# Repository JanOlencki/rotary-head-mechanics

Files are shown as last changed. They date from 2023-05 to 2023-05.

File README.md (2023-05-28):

# Mechanics of the Rotary Head
This repository is a part of a larger project. The description of it can be found in the [rotary-head-software](https://github.com/JanOlencki/rotary-head-software) repository.

## Features
* Two heads (azimuth and polarization)
* Stepper motor mounting
* Smooth rotation due to ball bearings
* 1:3.6 gear ratio (0.5° resolution when fully stepping a 200-step motor)
* Geodesy tribrach mounting
* Precise tribrach-based leveling
* RF connection via *Fairview Microwave SR1803* rotary joint
* Easily removable enclosure
* Enclosure compatible with the [Rotary Head Controller PCBs](https://github.com/JanOlencki/rotary-head-electronics)
* Laser holders used to position towers relative to each other

## Manufacturing
The original milled parts are made from nylon and steel without the use of numerically controlled machines. There are no tolerances marked or introduced in the models of these parts.

The enclosures and holders are printed from PETG. The models of the 3D printed parts include small gaps, that allows you to simply print and fit these parts with virtually no modification.

## Repository contents
* Separate Bills of Materials for each Rotary Head
* Models of the milled parts in the STEP format
* Models of the 3D printed parts in the STEP format
* Photos and renders

# Photos 
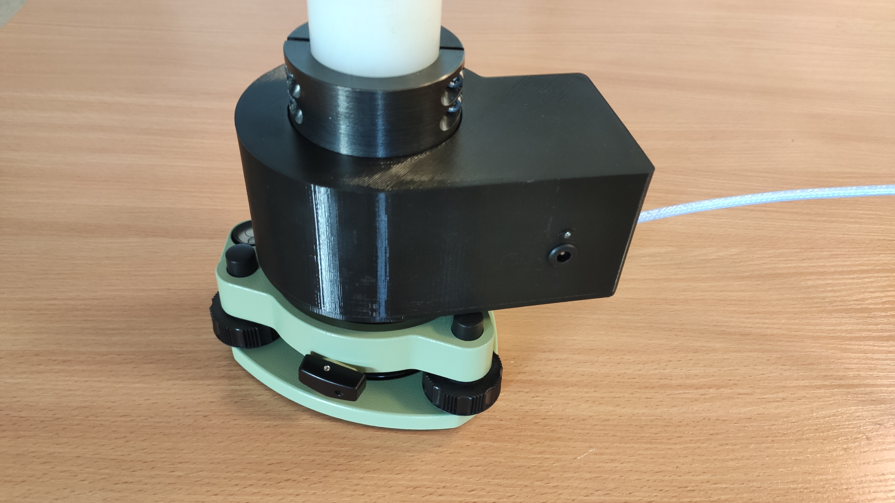
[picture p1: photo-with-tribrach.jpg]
Photo of the azimuth Rotary Head on the tribrach


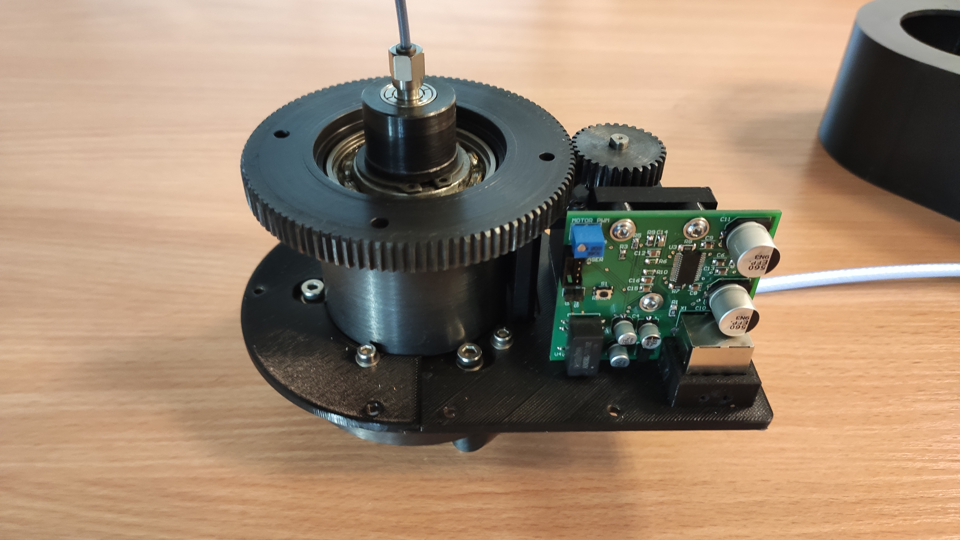
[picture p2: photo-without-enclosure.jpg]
Photo of the azimuth Rotary Head without enclosure


# Renders
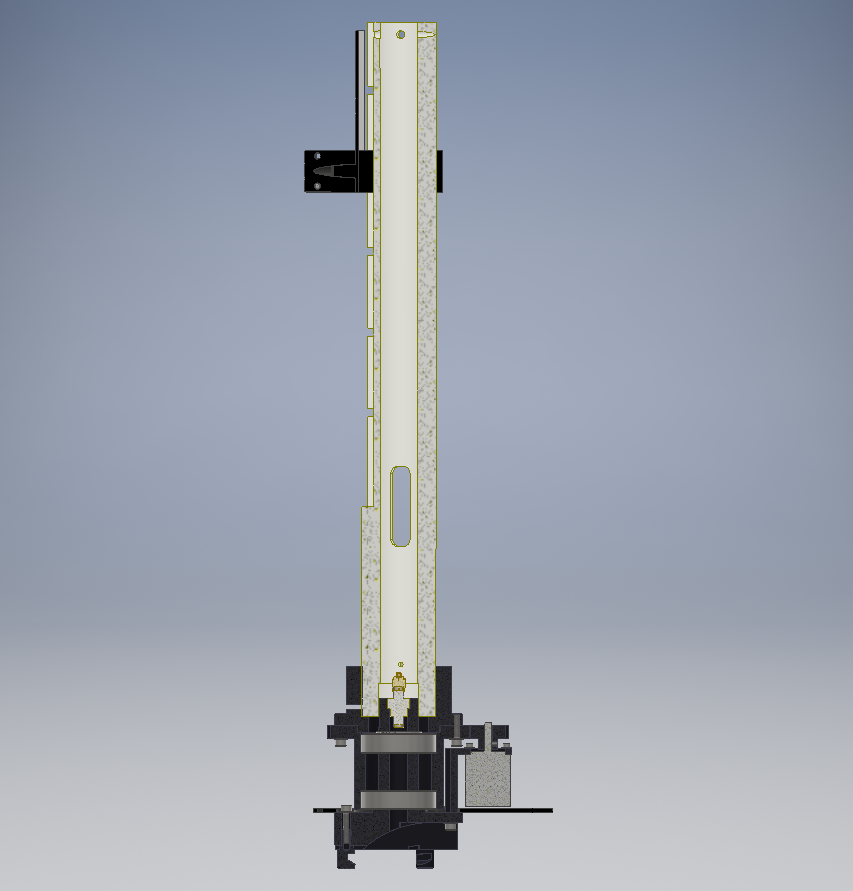
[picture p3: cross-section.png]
The cross section of Rotary Head


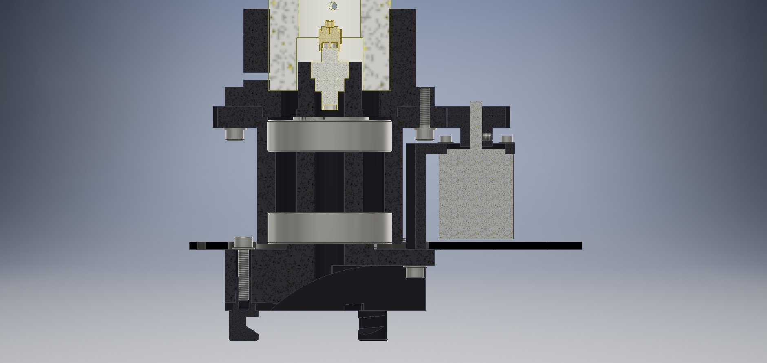
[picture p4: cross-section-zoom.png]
The zoomed cross section of Rotary Head


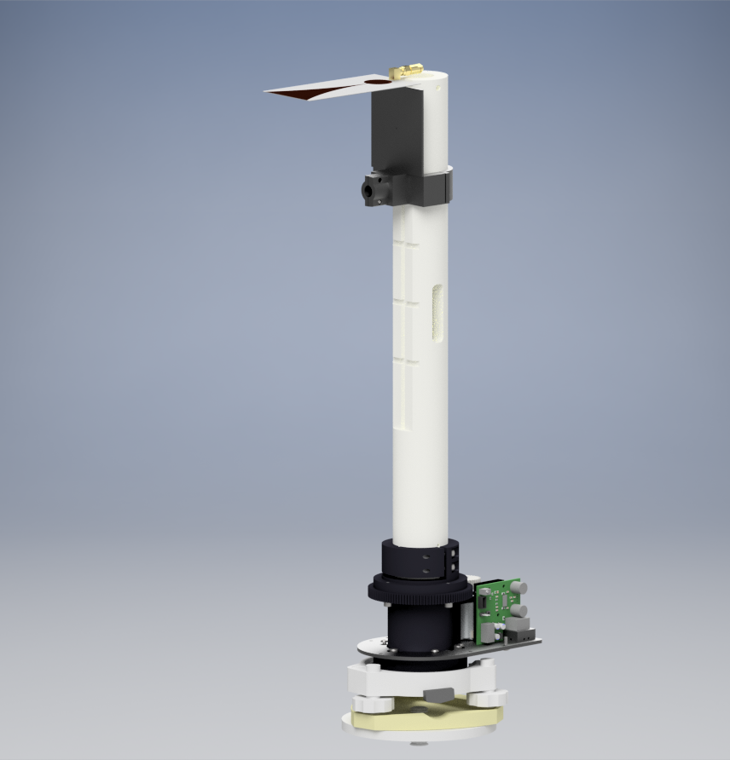
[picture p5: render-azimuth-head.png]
The render of the azimuth Rotary Head


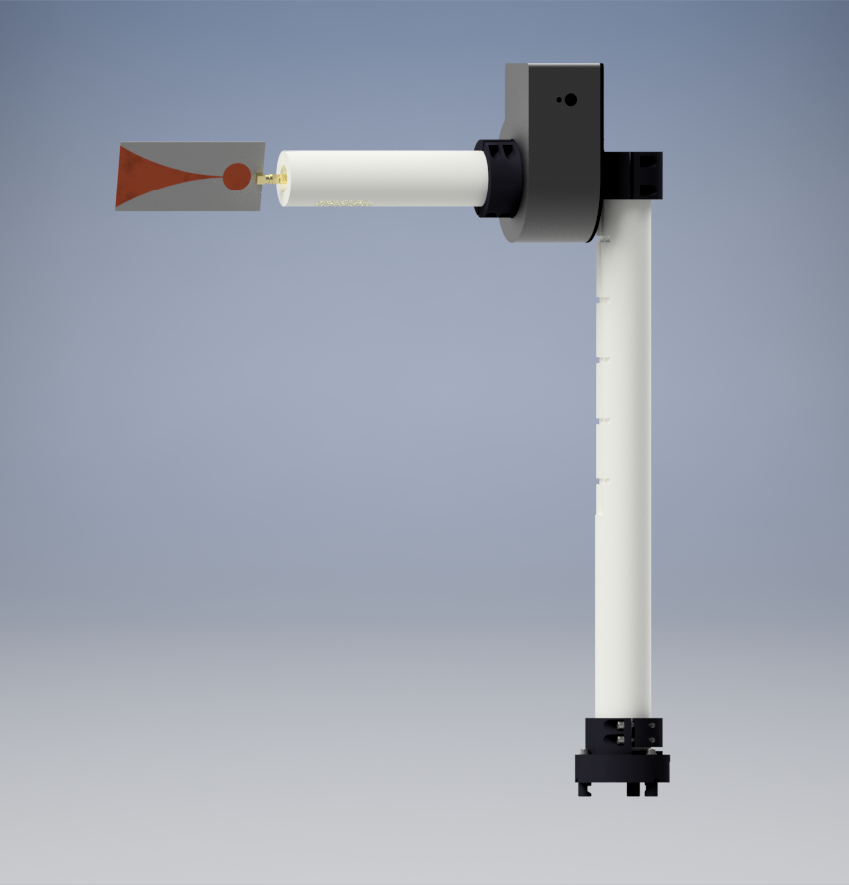
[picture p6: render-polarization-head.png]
The render of the polarization Rotary Head


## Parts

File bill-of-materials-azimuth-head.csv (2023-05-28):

Name | Quantity | Description | Comment
Flanged Button Screw M3 x 10mm (ISO 7380-2) | 15 | Used to screw the enclosure and milled parts together
Flanged Button Screw M3 x 10mm (ISO 7380-2) | 10 | Laser holder | Optional
Bearing 6005 - 25mm x 47mm x 12mm (DIN 625 - T1) | 2
Retaining ring 25mm x 1.2mm (DIN 471) | 1
Bolt M4 x 20mm (DIN 912) | 9
Bolt M4 x 16mm (DIN 912) | 4 | Used to bolt the outer sleeve and shaft holder together
Plain washer 4.3mm (DIN 125-1) | 13
Step motor Pololu 1205 | 1
Socket set screw M3 x 4mm (DIN 913) | 2 | Used to hold the rotary joint and to mount the gear to the motor shaft
Bolt M2.5 x 8mm (DIN 912) | 4 | Used to mount the motor
Plain washer 2.7mm (DIN 125-1) | 4
Rotary joint SR1803 | 1
Azimuth head shaft | 1 | Milled nylon part
Sleeve with gear | 1 | Milled steel part
Azimuth head tribrach adapter | 1 | Milled steel part
Gear | 1 | Milled steel part
Motor mount | 1 | Milled steel part
Shaft mount | 1 | Milled steel part
Tribrach stud | 3 | Milled steel part
Azimuth head enclosure bottom part 1 | 1 | 3d printed part
Azimuth head enclosure bottom part 2 | 1 | 3d printed part
Head enclosure top | 1 | 3d printed part
PCB holder | 1 | 3d printed part
Laser holder part 1 | 1 | 3d printed part | Optional
Laser holder part 2 | 1 | 3d printed part | Optional
Laser holder part 3 | 1 | 3d printed part | Optional
Laser holder part 4 | 1 | 3d printed part | Optional
Laser holder part 5 | 1 | 3d printed part | Optional

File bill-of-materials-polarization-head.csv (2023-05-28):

Name | Quantity | Description | Comment
Flanged Button Screw M3 x 10mm (ISO 7380-2) | 15 | Used to screw the enclosure and milled parts together
Flanged Button Screw M3 x 10mm (ISO 7380-2) | 10 | Laser holder | Optional
Bearing 6005 - 25mm x 47mm x 12mm (DIN 625 - T1) | 2
Retaining ring 25mm x 1.2mm (DIN 471) | 1
Bolt M4 x 20mm (DIN 912) | 13
Bolt M4 x 16mm (DIN 912) | 4 | Used to bolt the outer sleeve and shaft holder together
Plain washer 4.3mm (DIN 125-1) | 17
Step motor Pololu 1205 | 1
Socket set screw M3 x 4mm (DIN 913) | 2 | Used to hold the rotary joint and to mount the gear to the motor shaft
Bolt M2.5 x 8mm (DIN 912) | 4 | Used to mount the motor
Plain washer 2.7mm (DIN 125-1) | 4
Rotary joint SR1803 | 1
Polarization head vertical shaft | 1 | Milled nylon part
Polarization head horizontal shaft long | 1 | Milled nylon part
Polarization head horizontal shaft medium | 1 | Milled nylon part | Optional
Polarization head horizontal shaft short | 1 | Milled nylon part | Optional
Sleeve with gear | 1 | Milled steel part
Polarization head tribrach adapter | 1 | Milled steel part
Polarization head central part | 1 | Milled steel part
Gear | 1 | Milled steel part
Motor mount | 1 | Milled steel part
Shaft mount | 1 | Milled steel part
Tribrach stud | 3 | Milled steel part
Polarization head enclosure bottom part 1 | 1 | 3d printed part
Polarization head enclosure bottom part 2 | 1 | 3d printed part
Head enclosure top | 1 | 3d printed part
PCB holder | 1 | 3d printed part
Laser holder part 1 | 1 | 3d printed part | Optional
Laser holder part 2 | 1 | 3d printed part | Optional
Laser holder part 3 | 1 | 3d printed part | Optional
Laser holder part 4 | 1 | 3d printed part | Optional
Laser holder part 5 | 1 | 3d printed part | Optional

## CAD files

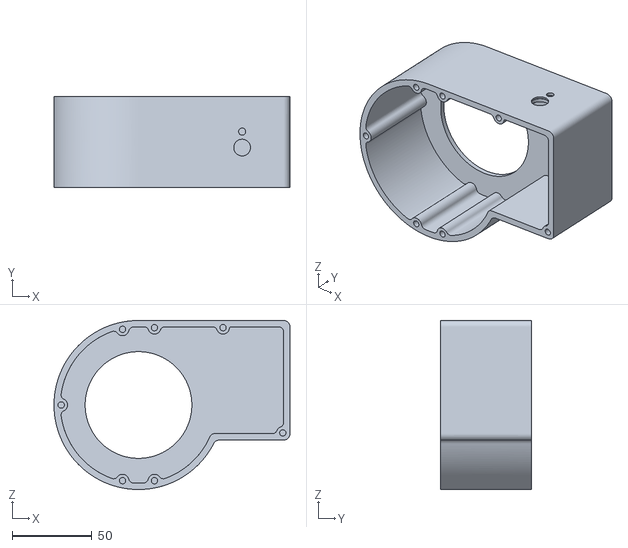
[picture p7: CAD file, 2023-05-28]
3d-printed/head-enclosure-top.stl
148.0 x 57.0 x 106.0

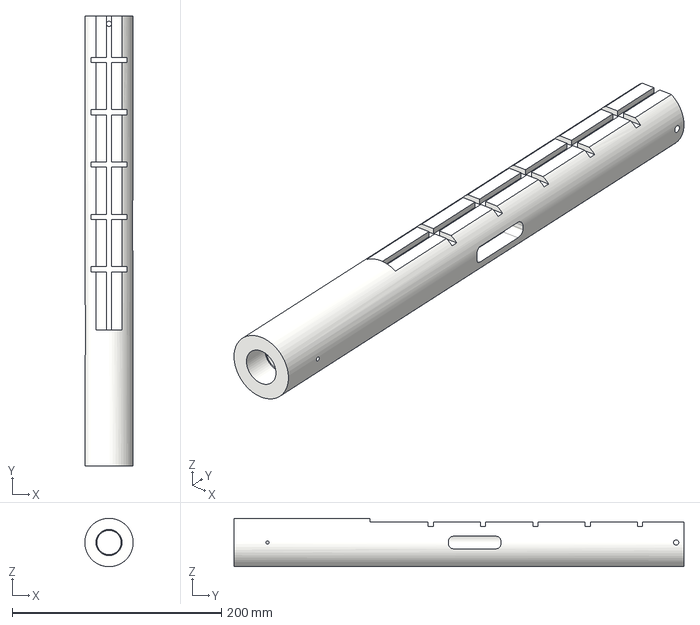
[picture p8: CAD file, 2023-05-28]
milled-parts/azimuth-head-shaft.stp
46.2 x 430.0 x 46.2 mm

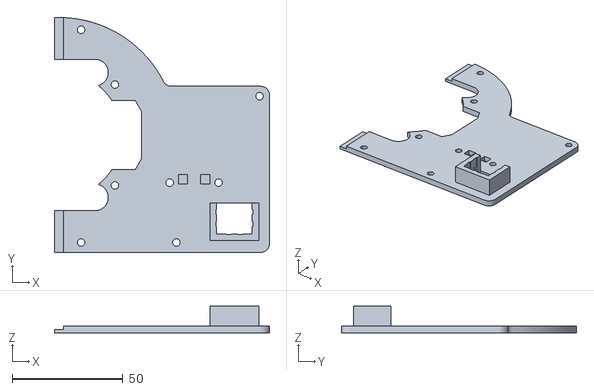
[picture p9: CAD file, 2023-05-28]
3d-printed/azimuth-head-enclosure-bottom-part-1.stl
97.0 x 106.0 x 12.0

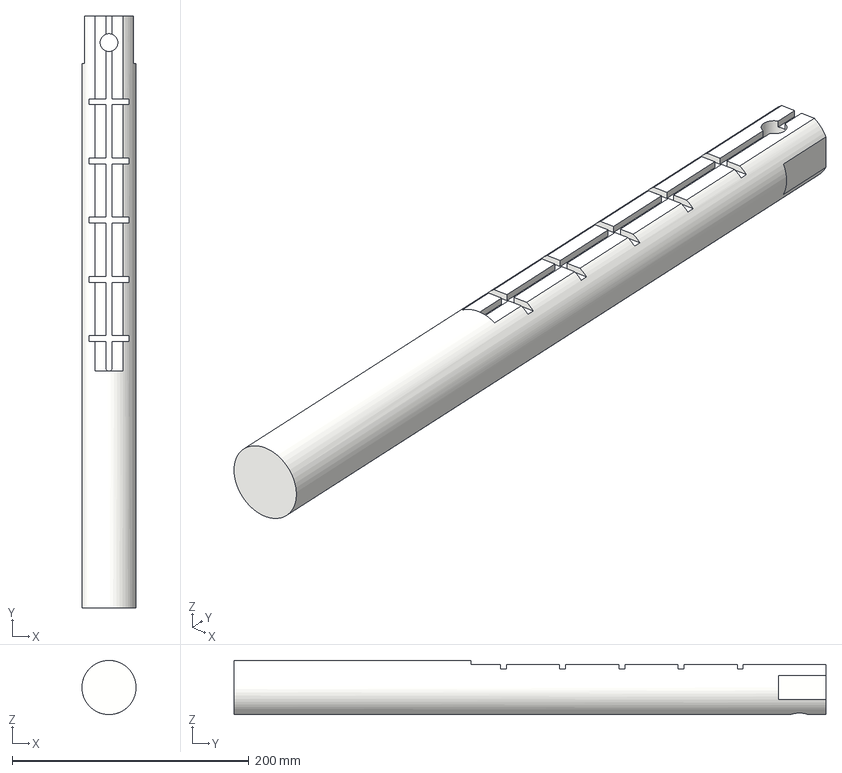
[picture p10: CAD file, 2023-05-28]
milled-parts/polarization-head-vertical-shaft.stp
45.8 x 500.0 x 45.7 mm

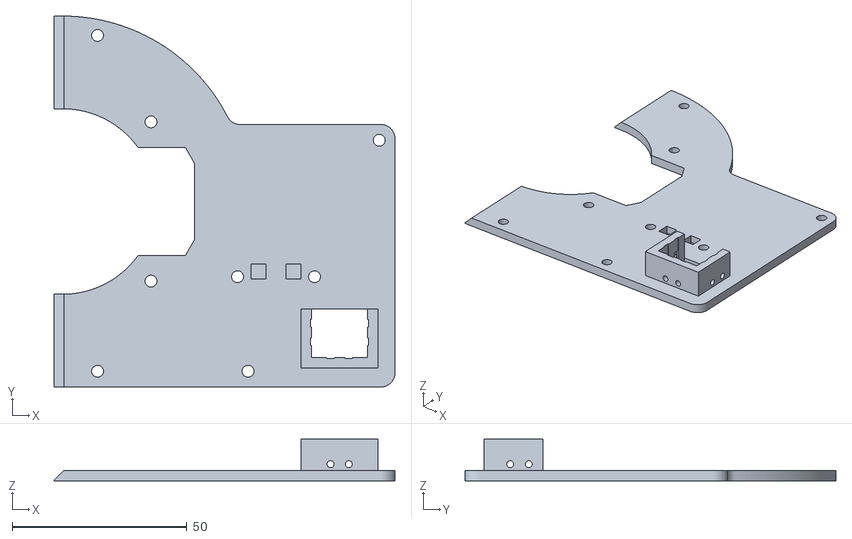
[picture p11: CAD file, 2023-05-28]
3d-printed/polarization-head-enclosure-bottom-part-1.stl
97.5 x 106.0 x 12.0

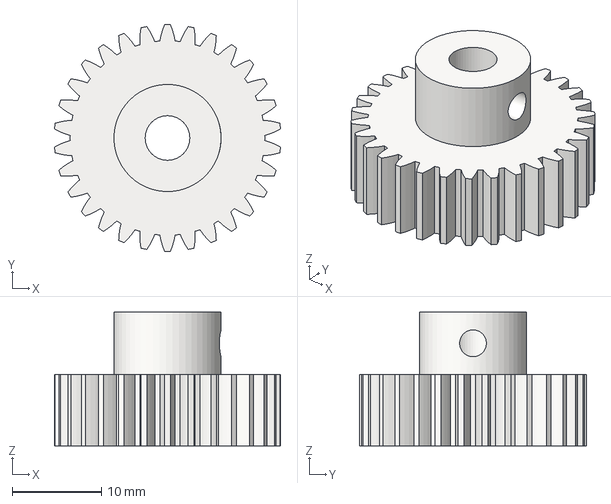
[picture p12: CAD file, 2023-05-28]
milled-parts/gear.stp
25.3 x 25.4 x 15.0 mm

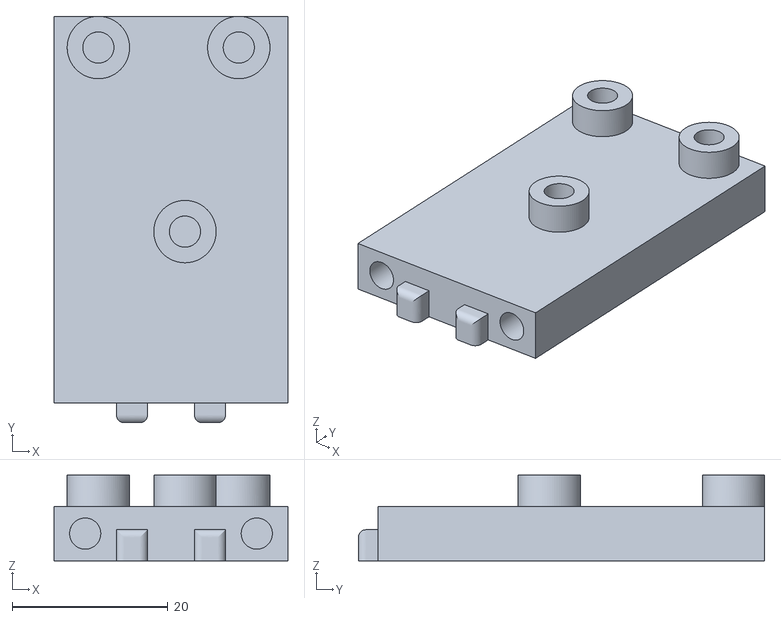
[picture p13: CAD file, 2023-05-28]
3d-printed/pcb-holder.stl
30.0 x 52.1 x 11.0

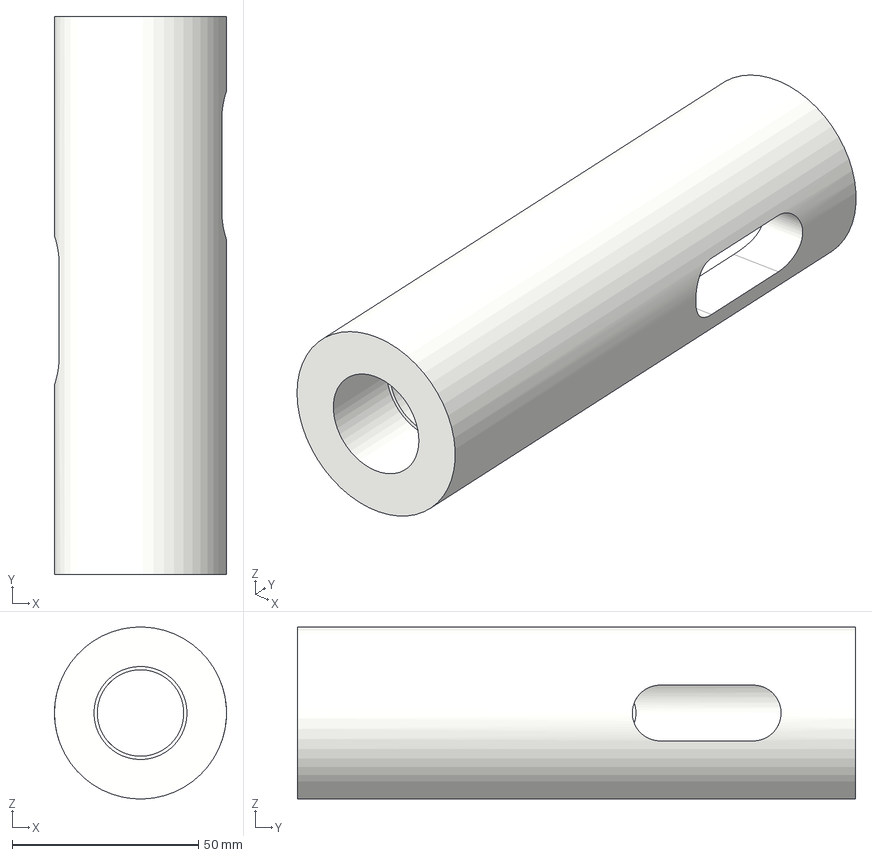
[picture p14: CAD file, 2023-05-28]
milled-parts/polarization-head-horizontal-shaft-medium.stp
46.2 x 150.0 x 46.2 mm

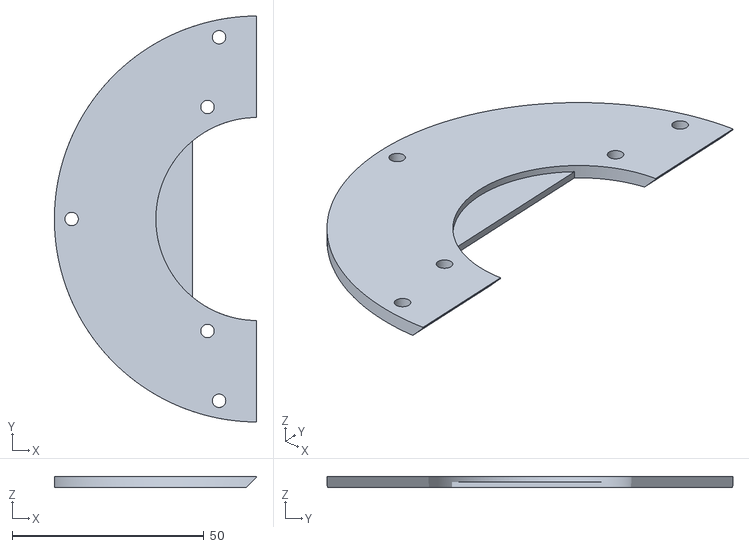
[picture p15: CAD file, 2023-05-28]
3d-printed/polarization-head-enclosure-bottom-part-2.stl
52.8 x 106.0 x 3.00

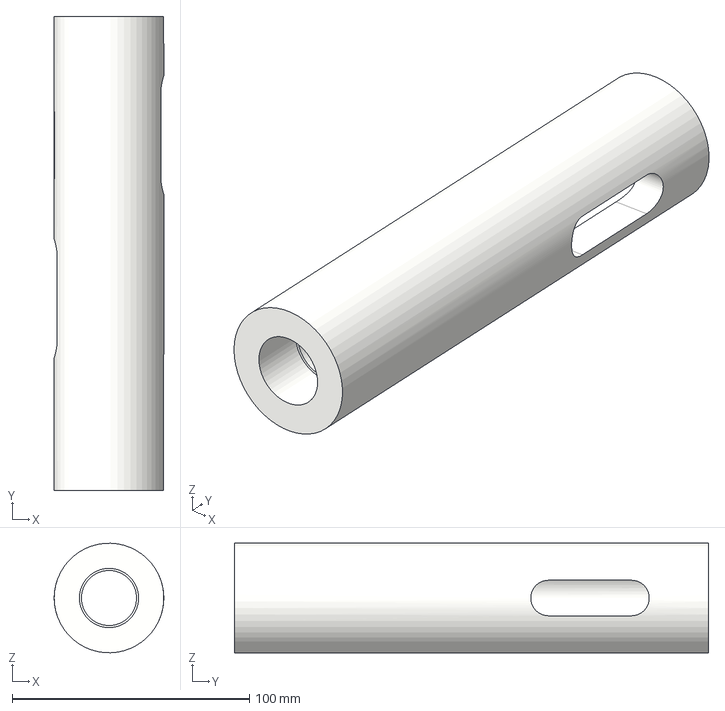
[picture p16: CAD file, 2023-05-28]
milled-parts/polarization-head-horizontal-shaft-long.stp
46.2 x 200.0 x 46.2 mm

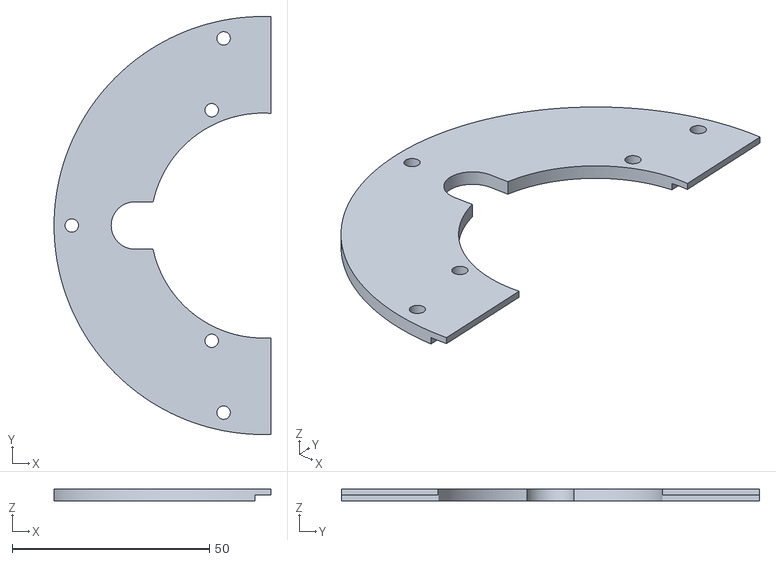
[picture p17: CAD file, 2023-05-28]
3d-printed/azimuth-head-enclosure-bottom-part-2.stl
55.0 x 106.0 x 3.00

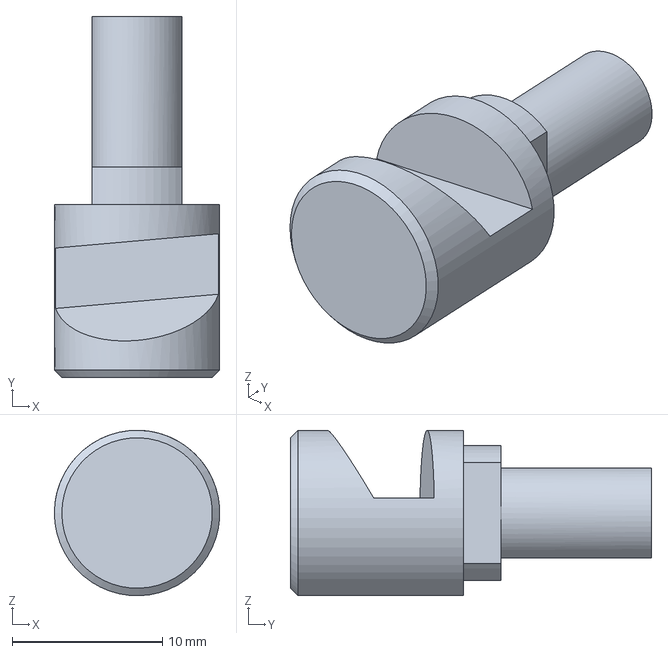
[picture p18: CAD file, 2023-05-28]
milled-parts/tribrach-stud.stp
11.0 x 24.0 x 11.0 mm

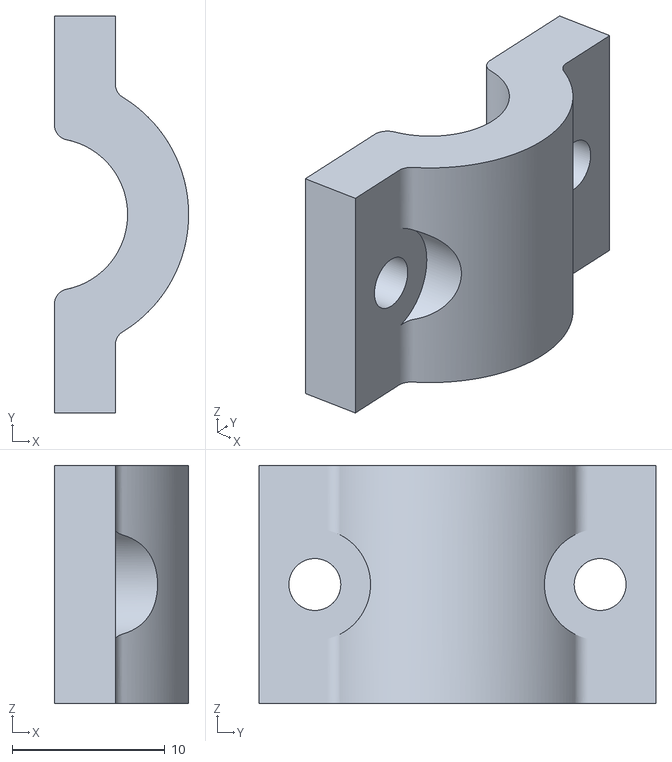
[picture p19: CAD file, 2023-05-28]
3d-printed/laser-holder-part-3.stl
8.80 x 26.0 x 15.6

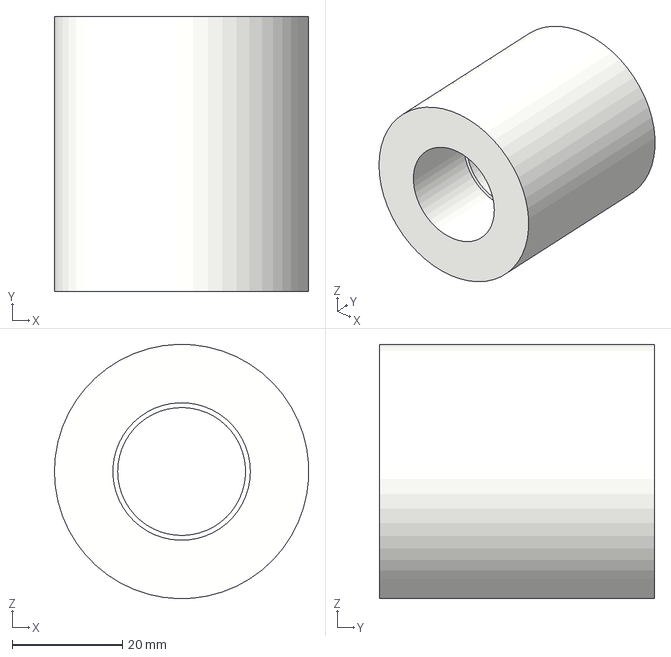
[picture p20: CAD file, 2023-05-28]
milled-parts/polarization-head-horizontal-shaft-short.stp
46.2 x 50.0 x 46.2 mm

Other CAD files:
3d-printed/laser-holder-part-1.stl
milled-parts/azimuth-head-tribrach-adapter.stp
3d-printed/laser-holder-part-4.stl
milled-parts/polarization-head-central-part.stp
3d-printed/laser-holder-part-2.stl
3d-printed/laser-holder-part-5.stl
milled-parts/motor-mount.stp
milled-parts/polarization-head-tribrach-adapter.stp
milled-parts/shaft-mount.stp
milled-parts/sleeve-with-gear.stp
